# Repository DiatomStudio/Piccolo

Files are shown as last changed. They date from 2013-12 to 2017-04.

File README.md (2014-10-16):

#Piccolo, the tiny cnc bot#

A pocket sized open source CNC-bot.

Using laser-cutting, off-the-shelf hardware and Arduino, you can make your own simple 3 axis robot. Attach a brush or pen to make a quick drawing robot, or extend Piccolo with sensors, custom toolheads, or by using multiple Piccolos together. Experiment with 2D or 3D digital fabrication at a small scale!

For more info please see [www.piccolo.cc](http://www.piccolo.cc)

[Piccolo Flickr Pool](http://www.flickr.com/groups/1929303@N21/)

[www.diatom.cc](http://www.diatom.cc)



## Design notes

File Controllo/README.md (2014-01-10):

# Controllo
----------------
Controllo is a standalone program that runs on your, pc , mac or linux machine. That lets you send your own SVG vector artworks or a series of pre-defined generative artworks to your Piccolo for drawing.

Your Piccolo will need to have the usbTether firmware installed and be attached to your computer in order to communicate with Controllo. The usbTether program can be found in [PiccoloLib](https://github.com/DiatomStudio/Piccolo/tree/master/PiccoloLib) under examples.
 

####installing
- Download Controllo_current.zip
- Unzip and run the appropriate application for your system.

####how to use
- Load your own svg or select a generative pattern using the buttons on the left. 
- Lower your piccolo's drawing impliment to the paper using either the thumbwhere on the side of the Piccolo or the UP_ DOWN_ buttons in Controllo.
- Press the STARRT button or button_1 on your Piccolo to start drawing. 

####hacking
Controllo is written using the Processing programming language. If you would like to make your own changes you will need.

- Processing: <http://processing.org/>

the following processing libraries

- controlP5: <http://www.sojamo.de/libraries/controlP5/>
- Geomerative: <http://www.ricardmarxer.com/geomerative/>

####notes
To correctly draw imported SVG drawings, SVG's should be exported with all lines expanded and no compound shapes. 

The svg size should be less than 300 x 300 px. 

Piccolo should be connected to your computer via usb before starting Controllo. 

Controllo and it's source code is a work in progress, most functions work however there will some bugs.

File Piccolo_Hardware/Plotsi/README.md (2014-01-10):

## Plotsi

Plotsi is a series of earlier Piccolo designs that started as 3d printed parts and changed to be laser cut.
Rather than the X > Y > Z configuration of the Telaio and Piccolo v1 versions, the Plotsi designs put the Y axis mounted on Z axis, ie: X > Z > Y.

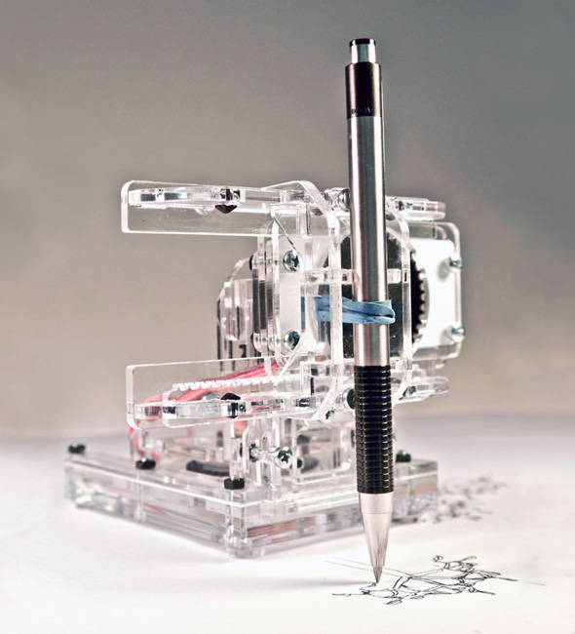
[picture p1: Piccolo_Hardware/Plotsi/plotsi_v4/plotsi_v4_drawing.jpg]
plotsi


---

### Plotsi v1

Early concept block-model looking at the dimensions of submicro servos and range of motion.  A speculative "cnc shield" for an arduino.  Not a working model, but could be with a bit of work.

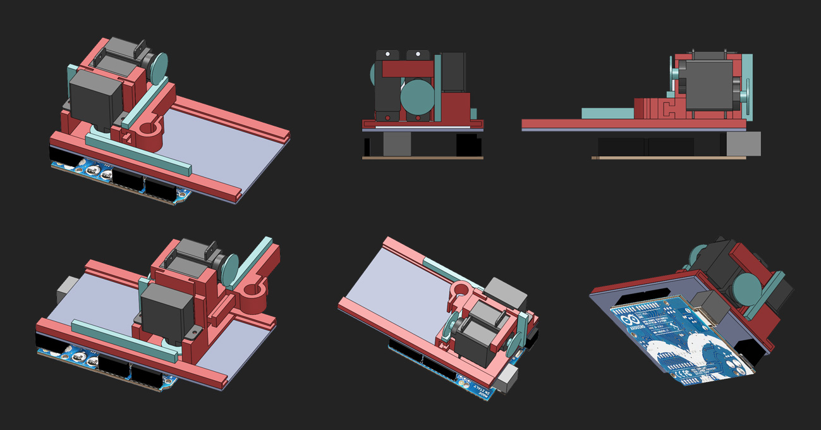
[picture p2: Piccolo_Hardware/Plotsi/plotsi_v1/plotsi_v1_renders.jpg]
plotsi-v1


---

### Plotsi v2

3D printable prototype, printed on on a makerbot cupcake cnc and with cheap generic analog servos (towerpro sg50-like).  Has a small 25x25x25mm output envelope.
[Youtube playlist of prototype in action](http://www.youtube.com/watch?v=IYrCUkX8gOE&list=PLRpx_txK6uzyulC7kqCXAvBz_-7jgT4Fn)

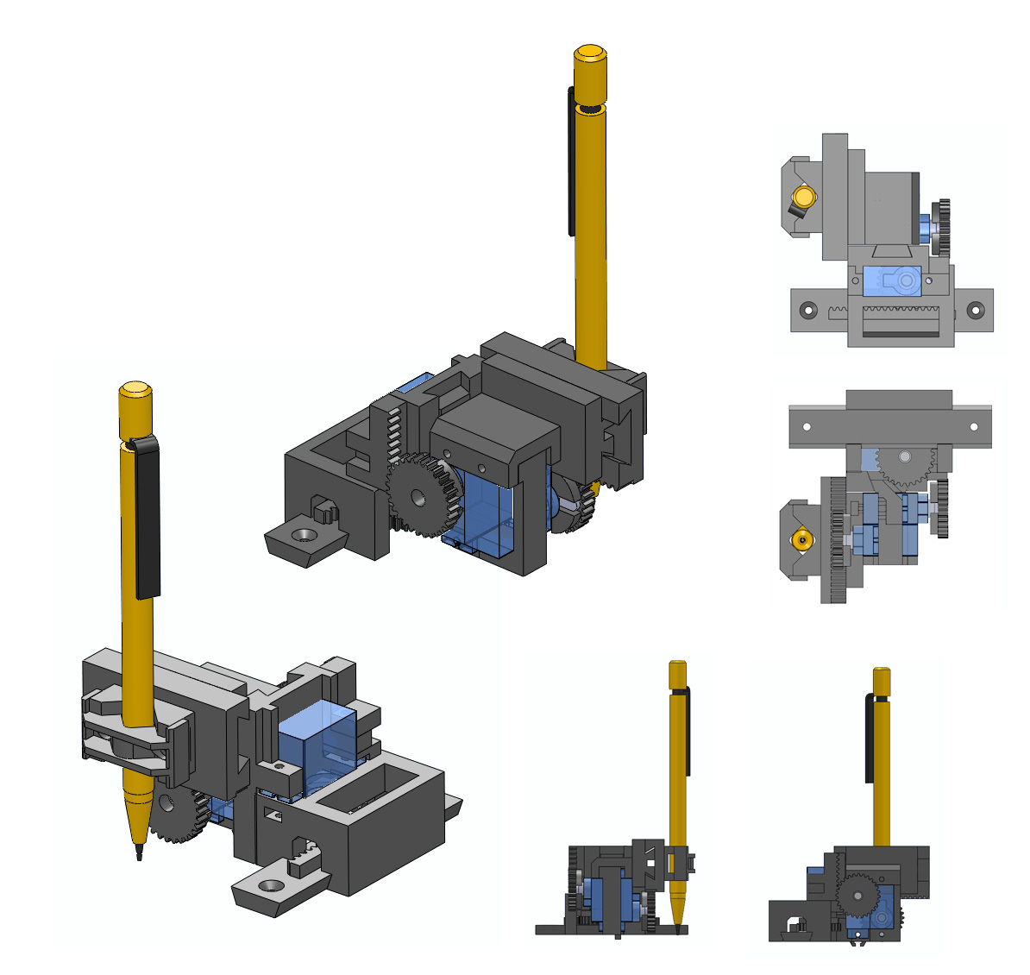
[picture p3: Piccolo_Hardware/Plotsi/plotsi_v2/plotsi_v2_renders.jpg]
plotsi-v2


---

### Plotsi v3

3D printable, also prototyped on a cupcake cnc but with less cheap emax digital ES08D servos.  Considerably larger than v2 with an output envelope of around 50x50x30mm roughly.

Used for an [installation at Tangíveis Resiência AZ](http://blog.diatom.cc/piccolo/piccolo-prototype-plotsi-at-tangiveis-residencia) in 2012, together with Teresa Cardoso.

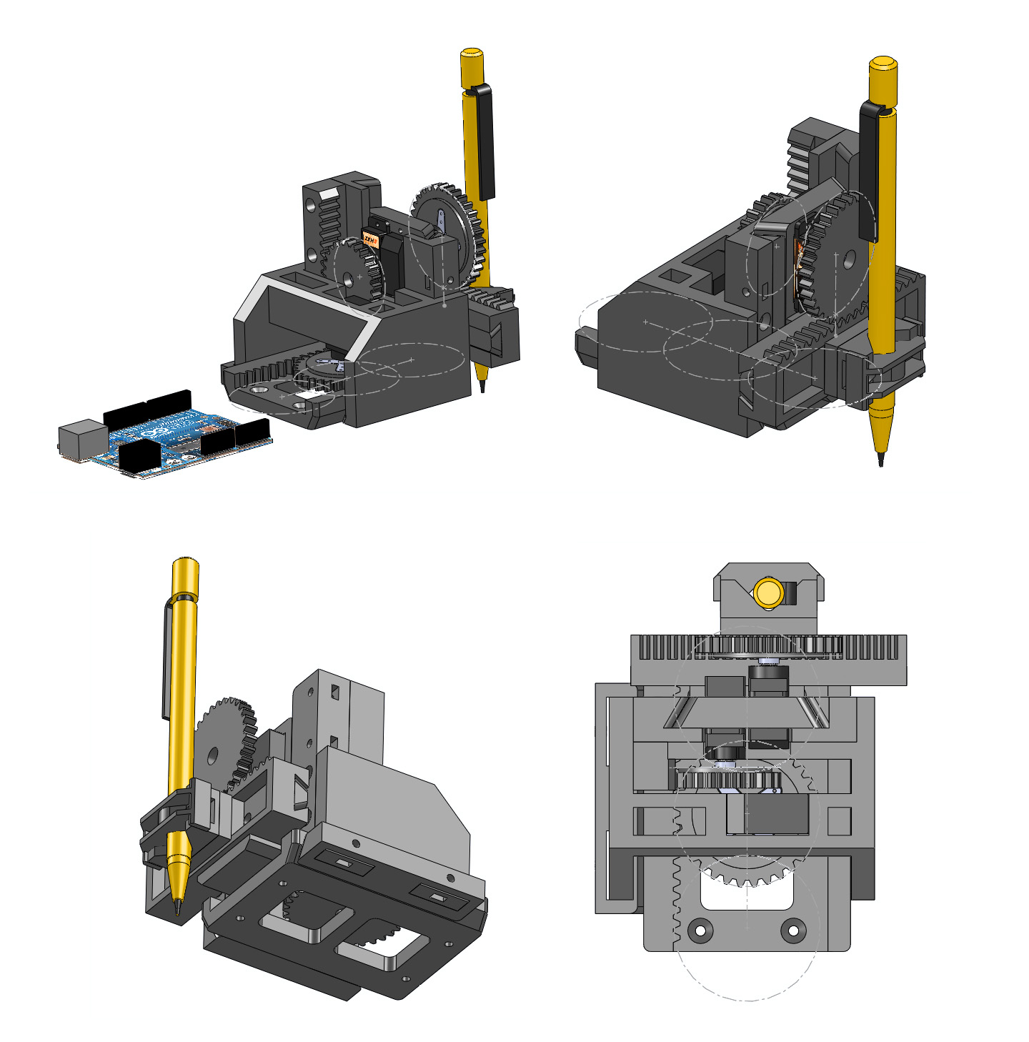
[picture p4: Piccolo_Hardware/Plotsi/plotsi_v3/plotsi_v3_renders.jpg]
plotsi-v3


---

### Plotsi v4

Laser cut design published with the initial launch of [](www.piccolo.cc).  Uses the same emax servos and has a larger 65x65x30mm output envelope.  This was our first widely prototyped Piccolo version.

[Winner of the TEI 2012 design challenge](http://blog.diatom.cc/piccolo/piccolo-wins-the-tei-design-challenge)

[Initial Piccolo cnc video](https://vimeo.com/36869769)

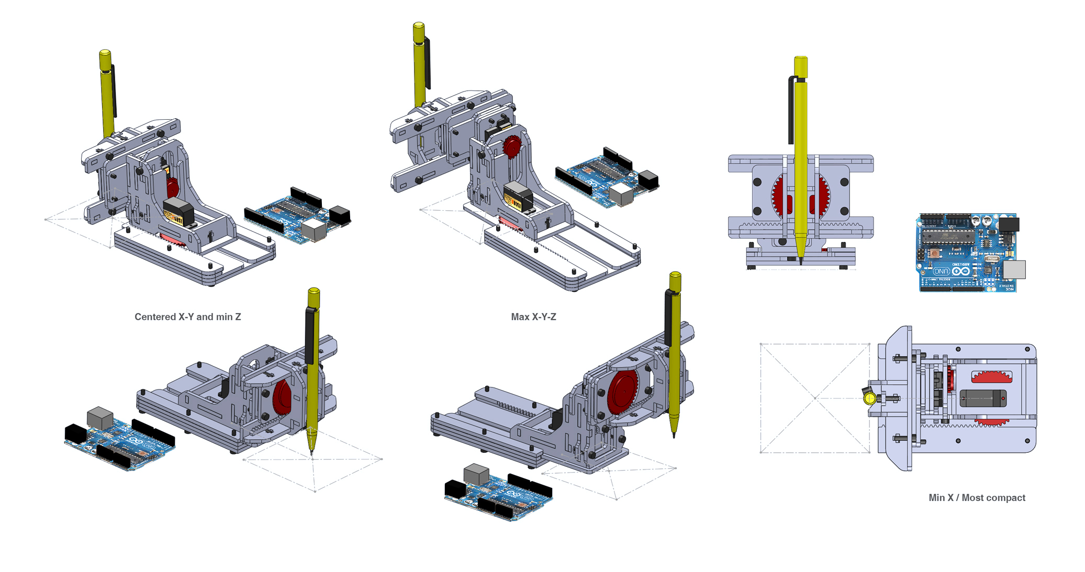
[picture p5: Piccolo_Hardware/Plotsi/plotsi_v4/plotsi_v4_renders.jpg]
plotsi-v4


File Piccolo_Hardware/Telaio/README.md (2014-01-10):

## Telaio

Telaio ("frame") follows an X > Y > Z configuration that stacks the X and Y gears on top of each other.  This is the strategy that led to the Piccolo v1 design.

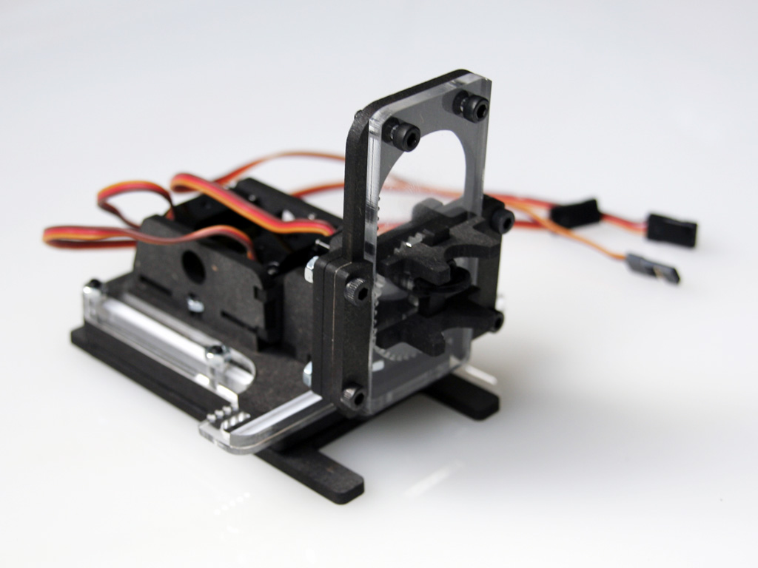
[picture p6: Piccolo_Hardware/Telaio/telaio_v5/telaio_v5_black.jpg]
telaio


---

### Telaio v0 / v1 / v2

These initial prototypes/concepts started with just the X/Y axis to create a simple servo-driven plotter.  The first was prototyped on a papercutter, the second was laser-cut.

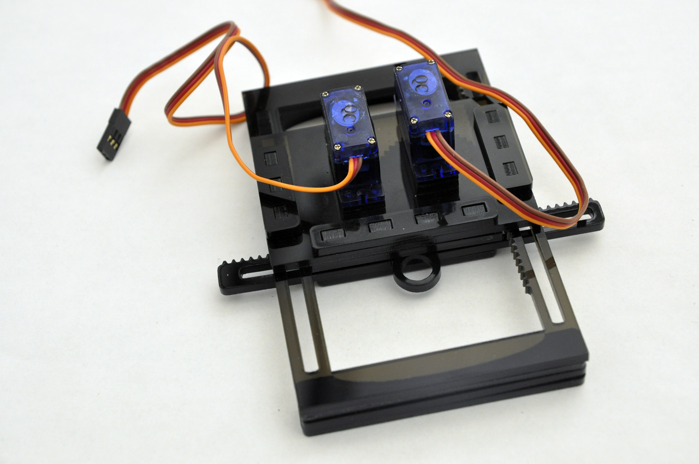
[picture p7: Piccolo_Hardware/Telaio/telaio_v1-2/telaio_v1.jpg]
telaio-v1


---

### Telaio v3 / v4

Laser-cut iterations using emax ES08D digital servos.

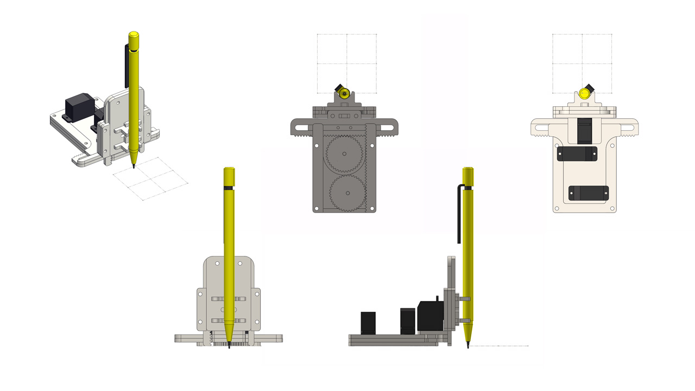
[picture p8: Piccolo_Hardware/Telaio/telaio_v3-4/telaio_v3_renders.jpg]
telaio-v3

_Telaio v3_

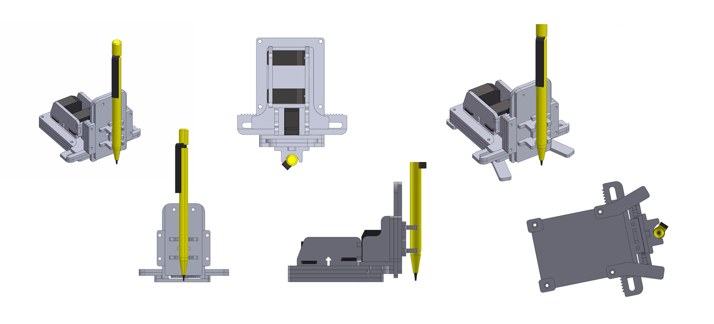
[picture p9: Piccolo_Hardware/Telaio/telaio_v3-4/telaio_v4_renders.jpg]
telaio-v4

_Telaio v4_

---

### Telaio v5

Smaller/more resolved laser-cut version, still using the ES08D servos.  The smallest of all our piccolo designs, but with an output envelope of about 60x60x40mm.

This design was used at our first piccolo workshop at the [LiWoLi 2012 festival in Linz](http://blog.diatom.cc/piccolo/build-your-own-piccolo-workshop-at-linz).  In the archive there are two versions of the design, one using M2 cap screws and one using more common, M3 ones.  As with Piccolo v1, we reccomend using a combination of MDF and acrylic as shown in the photo to help reduce friction.

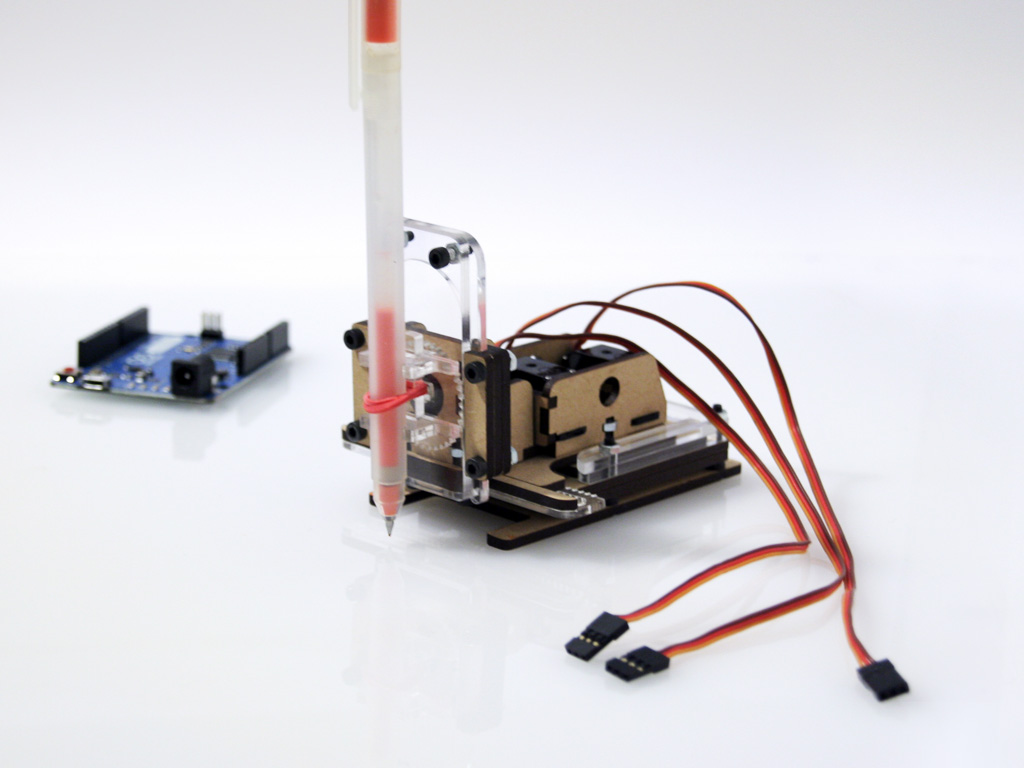
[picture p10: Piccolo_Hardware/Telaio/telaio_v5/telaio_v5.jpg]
telaio-v5


---

### Telaio v6

Laser-cut iteration that is a scaled-up version of v5 and using Corona DS-929MG servos.  We also integrated a Sparkfun Pro Micro into the base with a small protoboard for hooking up the servos, creating a 'stand-alone' design.  The output envelope is similar to the v5, about 60x60x45mm.

We used this design at our make-your-own-piccolo workshop at TEI 2013 in Barcelona.

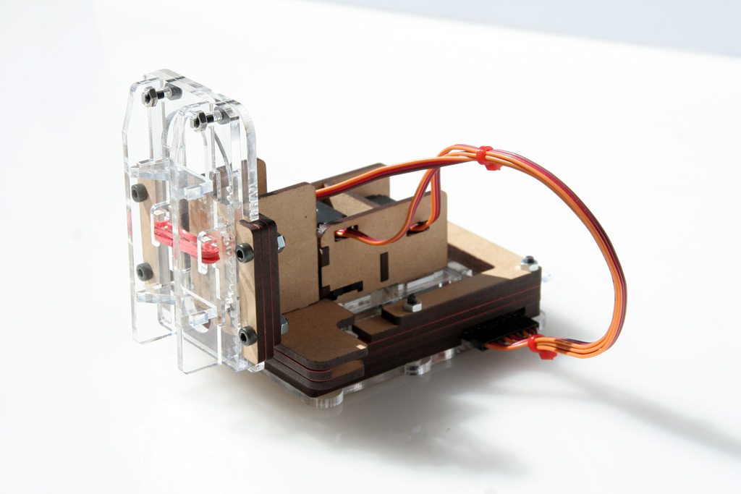
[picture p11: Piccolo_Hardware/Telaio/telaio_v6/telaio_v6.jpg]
telaio-v6


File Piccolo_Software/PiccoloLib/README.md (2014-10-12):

#PiccoloLib#

PiccoloLib is a library for [Arduino](http://www.arduino.cc) that makes it simple to program a Piccolo.

For an overview of PiccoloLib basics, take a look at [Getting Started](../../../../wiki/Getting-Started)

* Control movement, speed and accuracy.
* Various shape drawing functions.
* Configure & calibrate Piccolo.
* Send Piccolo co-ordinates over serial.
* [UsbTether](PiccoloLib/examples/usbTether/usbTether.ino) example lets you control piccolo from Processing using the PiccoloP5 library.
* Configure axes individually with PiccoloAxis class, or add additional axes.

---

##Installation##

1. Download PiccoloLib_current.zip
2. Open the zip in Arduino by: Sketch > Import Library > Add Library

Alternatively, you can extract the archive into into your Arduino libraries folder manually.
If you are not sure where your libraries folder is, have a look at the Arduino libraries guide: http://arduino.cc/en/Guide/Libraries

---

##Reference##

Piccolo's output is intended to be used in mm, however you can scale the output to any arbitrary units using *calibrate()*.

###PiccoloLib Class###

---
####Setup, Configuration & Motion####

`void setup()`  
Sets up piccolo using the default pin assignments for the servos:  
X pin 3  
Y pin 5  
Z pin 6

`void setup(int xPin, int yPin, int zPin)`  
Set up piccolo using custom pins assignments.

`void invert(boolean invertX, boolean invertY, boolean invertZ)`  
Invert the output on any of the axes.

`void moveCenter(float xOffset, float yOffset)`  
`void moveCenter(float xOffset, float yOffset, float zOffset)`  
Adjust piccolo's zero position.

`void calibrate(float targetDimension, float actualX, float actualY)`  
`void calibrate(float targetDimension, float actualX, float actualY, float actualZ)`  
Use this to scale piccolo's output, which you can use to calibrate its accuracy.  First draw a square (or cube) of *targetDimension*, then measure the output and put *calibrate()* into your *setup()* with these dimensions as *actualX*, *actualY* etc.

`void setBedSize(float size)`  
`void setBedSize(float xySize, float zSize)`  
`void setBedSize(float xSize, float ySize, float zSize)`  
Will set the minimum and maximum positions of each axis, therefore defining the overall bed size.

`void setSpeed(float speed)`  
Defines piccolo's movement speed when using vertex() or shape functions.  In mm per second.  Default speed is 60mm/s.

`void setStepSize(float _stepSize)`  
Steps are used to control piccolo's motion and speed.  The default step size is 0.1mm.  A smaller step size means a more controlled motion, but too small will limit the maximum speed.  
This also affects curvature when using *ellipse()*, *arc()*, or *bezier()* - a smaller stepSize means a less faceted curve

`int drawOrientation`  
`void setDrawOrientation(int _orientation)`  
**_Work in progress._** Rotates the output:  
0 - default, drawing with bottom of drawing to the left.  
1 - top, as if piccolo is drawing upside down.  
2 - right, drawing with the bottom of the drawing to the right.  
3  - bottom, as if piccolo is drawing the correct way up.  

`boolean disableMotion`  
Disables servo motion, for debugging purposes.

---
####Piccolo Inputs####

`float readThumbwheel()`  
Returns a value from 0 to 1023 based on the position of the thumbwheel.

`boolean buttonOneDown()`  
Returns true if button one is pressed.

`boolean buttonTwoDown()`  
Returns true if button two is pressed.

---
####Mechanical Control####

`void moveX(float x)`  
`void moveY(float y)`  
`void moveZ(float z)`  
`void move(float x, float y)`  
`void move(float x, float y, float z)`  
Sends the servo(s) to a position.  They will respond at their maximum speed, and you may need to allow time for the servos to move in your code with *delay()*.

`void home()`  
Moves piccolo to (X minimum, 0, pen-up position).

`void thumbwheelControlX()`  
`void thumbwheelControlY()`  
`void thumbwheelControlZ()`  
Will move piccolo in each axis based on the thumbwheel position, between the minimum and maximum.

`void setPenDownPos(float _penDownPos)`  
`float getPenDownPos()`  
Set or retrieve the pen-down position.

---
####Making Shapes####

In general all drawing commands follow the same format as Processing drawing commands, for more info on these please visit: http://processing.org/reference/

`void beginShape()`  
Moves piccolo to the first vertex and then lowers the pen to the pen-down position.  
`void endShape()`  
Raises the pen to the pen-up position.  

`void vertex(float x,  float y)`  
`void vertex(float x,  float y,  float z)`  
Moves piccolo to (x,y,z) using the step size and speed to control the motion.

`void line(float x1, float y1, float x2, float y2)`  
`void line(float x1, float y1, float z1, float x2, float y2, float z2)`  
`void rect(float x,  float y,  float width, float height)`  
`void rect(float x,  float y,  float z, float width, float height)`  
`void ellipse(float x,  float y,  float width, float height)`  
`void arc(float x , float y , float width, float height, float startA, float stopA)`  
`void bezier(float x1, float  y1, float  cx1, float  cy1, float  cx2, float  cy2, float  x2, float  y2)`  
`void bezierYZ(float x1, float  y1, float  cx1, float  cy1, float  cx2, float  cy2, float  x2, float  y2)`  
`float bezierPoint(float a, float b, float c, float d, float t)`  
`float bezierTangent(float a, float b, float c, float d, float t)`  

---
####Serial Communication####

`void serialSetup()`  
Opens a serial port at 115200 baud. ready for Piccolo instructions from Controllo or another host device. This is only needed if Piccolo is controlled remotely. 

`void serialLoop()`  
Main Serial loop, this should be called in program main loop to check for waiting piccolo instructions on the serial port. This is only needed if Piccolo is controlled remotely via Controllo or another host device. 

`boolean serialStream`  
A debug flag used to stream Piccolo's move coordinates back over serial for rendering in Controllo.  
This is also useful for retrieving coordinates from Piccolo to debug your toolpath.

---
###PiccoloAxis class###

Each servo is controlled as a PiccoloAxis object.  
*uS = pulse width in microseconds of signal sent to the servo.*

---
####Variable Heirarchy####

1. `uScenter` - Defines the center position of the servo, based on where we want piccolo think the center is.  Normally this would be mid-way between the minimum and maximum rotation of the servo.  Default is 1551uS.  
`bedSize` - We define what we want the bed size to be.  The default is 50mm, which is a conservative size that should fit within the range of most DS929-MG servos.  
`uSdeg` - We specify the change in uS per degree of rotation for the servo. This can be calibrated as in 5.  Default is 9.7 us/deg.  
`gearSize` - We specify the gear pitch diameter based on the actual pinion gear dimensions.  Default is 35.23mm.

2. The gear pitch diameter and the change in uS per degree are used to calculate the change in uS per mm of motion:  
`uSmm = uSdeg/((PI/360)*gearSize)`

3. The uS range is found by multiplying the bed size by the uS/mm:  
`uSrange = bedSize * uSmm`

4. The uS minimum and maximums are found by using the uS range and center:  
`uSmin = uScenter - (uSrange/2)`  
`uSmax = uScenter + (uSrange/2)`

5. uSdeg can be calibrated by drawing a target dimension and measuring the actual output:  
`uSdeg  = ((target*uSmm)/actual) * (PI/360)*gearSize`

---
####Setup, Configuration & Motion####

`void setup(int _pin)`  
`void setup(int _pin, int _uScenter, float _bedSize)`  
`void setup(int _pin, int _uScenter, float _bedSize, float _uSdeg)`  
`void setup(int _pin, int _uScenter, float _bedSize, float _uSdeg, float _gearSize)`  
`void setup(int _pin, int _uScenter, float _bedSize, float _uSdeg, float _gearSize, boolean _inverted)`

`void calcuSmm()`  
`void calcuSrange()`  
`void calcMinMax()`  
`void calcuSdeg(float target, float actual)`

`void invert(boolean _inverted)`  
`void moveCenter(float offset)`  
`void setBedSize(float newSize)`  
`void move(float _pos)`  

---
####Helper Functions####

`int getPin()`  
`int getuScenter()`  
`float getuSdeg()`  
`float getGearSize()`  
`float getBedSize()`  
`float getuSmm()`  
`int getuSrange()`  
`int getuSmin()`  
`int getuSmax()`  
`float getPos()`  
`boolean isInverted()`

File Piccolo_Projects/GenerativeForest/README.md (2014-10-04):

# Generative Forest
A Piccolo Project 
----------------

Piccolo is a pocket-sized stand-alone CNC platform.  For more info please see [www.piccolo.cc](http://www.piccolo.cc)

####About: 
Piccolo draws a generative forest across a table top.

Piccolo draws generative plants and trees using a light sensor as it's input. When Piccolo is placed under a bight light, taller and more bushy tree is generated and drawn while lower light levels or shadows result in small shrubs and grasses. 

####You Will Need:

- 1 x Piccolo
- 1 x LDR (Light dependent resistor)
- 1 x Resistor matching maximun LDR value e.g.e 10K 

- PiccoloLib (tested with v0.8)
- GenerativeForest Arduino sketch

####Assembley: 

Wire your LDR with one leg connected to the A2 input on the side of your piccolo and the other connected to GND, now take your resistor and connect one end to VCC and the other also to A2.

This has created a voltage divider so if more light is hits the LDR it's resistance will lower allowing current to flow into GND instead of A2 a darker environment will cause the LDR's resistance to raise and more current to flow into A2 resulting in  a higher reading. 

The LDR can be placed at other points on Piccolo for example the Z-Axis by soldering wires to it's legs. 

Make sure PicccoloLib is installed correctly and upload the GenerativeForest Sketch to piccolo. 

####Usage: 

- Add a drawing implement to Piccolo and set the drawing height using the thumb wheel. 
- Place Piccolo under the darkest point of light on the surface and hold down button two for two seconds (the button next to the usb plug) this calibrates you light sensor.
- Move piccolo onto a surface and press button one to start drawing a generative tree.

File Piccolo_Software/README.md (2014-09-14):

# Piccolo Software
----------------

### Controllo
----------------
Controllo is a standalone program that runs on your, pc , mac or linux machine. That lets you send your own SVG vector artworks or a series of pre-defined generative artworks to your Piccolo for drawing.

### PiccoloLib
----------------
PiccoloLib is a Arduino library for controlling Piccolo using Arduino and Processing like drawing calls. 

#####usbTether src
PiccoloLib includes an example program (sketch) 'usbTether'. This sketch needs to be uploaded to your Piccolo in order to use Controllo or PiccoloP5 with your Piccolo. 

### PiccoloP5
----------------
PiccoloP5 is a Processing library for controlling your Piccolo from your computer in real time. Processing drawing commands can be sent to your Piccolo for drawing. 

#####Controllo src
Controllo is included as example in the PiccoloP5 library.

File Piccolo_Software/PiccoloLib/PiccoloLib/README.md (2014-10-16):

##PiccoloLib v0.81  
*Arduino library for controlling Piccolo, the tiny CNC-bot.*  

Piccolo.cc  
Created by Diatom Studio, October 10, 2013.  
Released into the public domain.  

##Changes:

###0.82  
- Fixing bugs in examples.
- Removed incompatible examples. 

###0.81  
-  Minor restructuring of comments. 
-  Added bezier(y,z) function
-  Commented out unused Piccolo Axis functions.s

###0.8  
-  Major restructuring of code. 
-  Added Axis objects to store and calculate Axis positions. 

###0.21  
-  Reverted BeginShape and EndShape back to BeginDraw and EndDraw to bring them in line with processing.org
-  Changed received coordinates from human readable chars to signed 32 bit ints backed into 4 bytes. This make our ranges larger, supports negative numbers and we send less data. 

###0.2  
-  Start of change tracking.

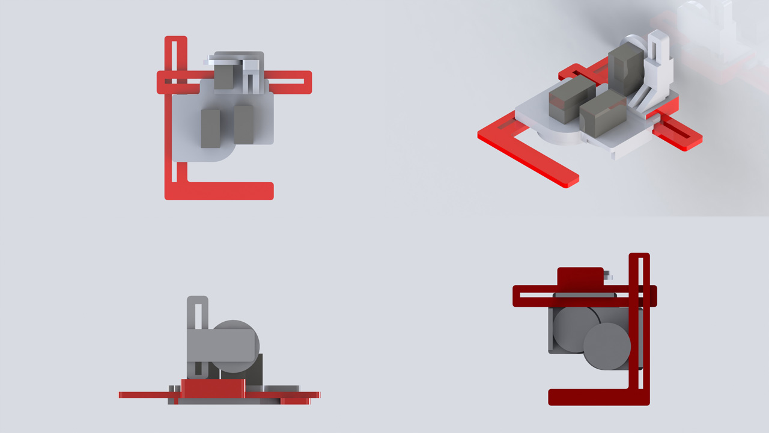
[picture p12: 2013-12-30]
Piccolo_Hardware/Telaio/telaio_v1-2/telaio_v2_renders.jpg

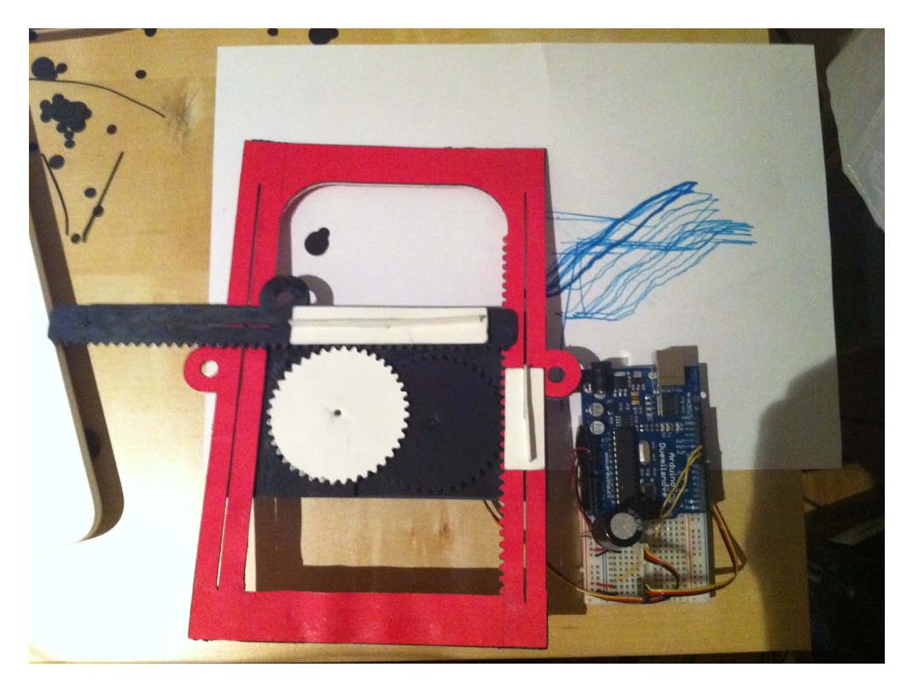
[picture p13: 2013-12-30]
Piccolo_Hardware/Telaio/telaio_v1-2/telaio_v0.jpg

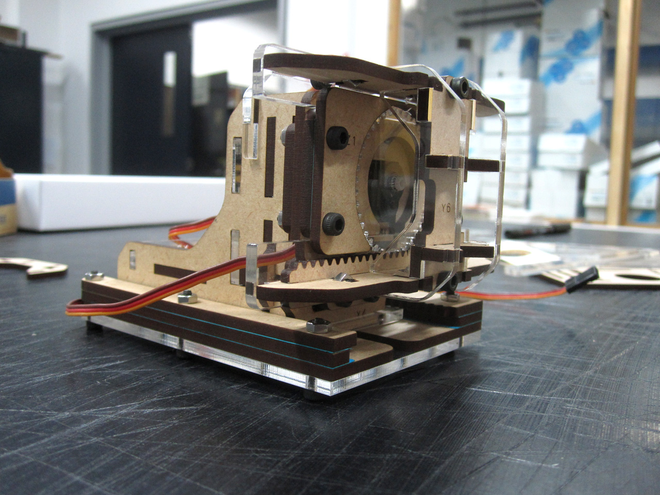
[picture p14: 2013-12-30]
Piccolo_Hardware/Plotsi/plotsi_v4/plotsi_v4.jpg

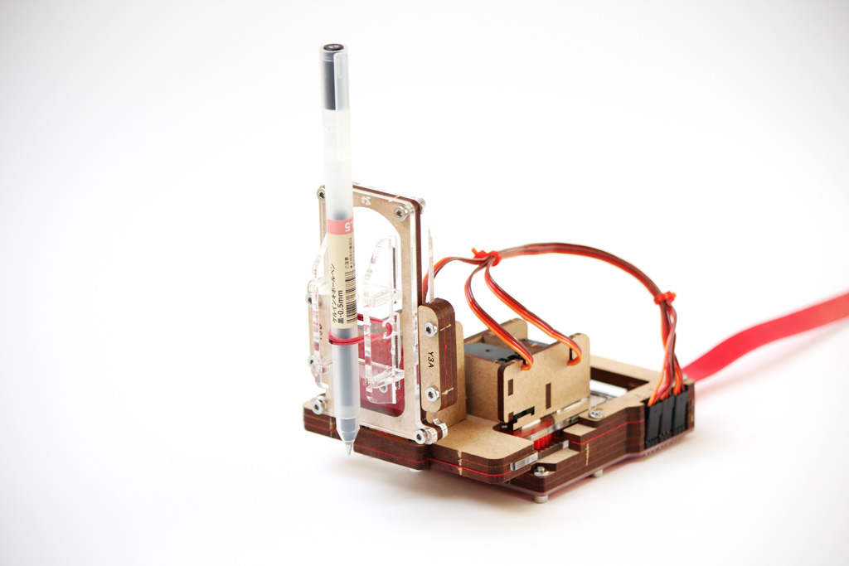
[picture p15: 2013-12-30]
Piccolo_Hardware/Piccolo_v1/piccolo_v1.jpg

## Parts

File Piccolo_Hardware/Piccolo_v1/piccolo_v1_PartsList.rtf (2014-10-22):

Piccolo v1 Parts List

Servos
3x Corona DS-929MG
http://www.servodatabase.com/servo/corona/ds-929mg

Material
3mm Acrylic, about 200 x 200
3mm MDF, about 200 x 270
Heavy Paper, about 160gsm, about 150 x 130

Fasteners

Metric Sockethead Cap Screws :

8x M3 10mm with low profile head
3x M3 16mm with low profile head
2x M3 10mm with normal head
4x M3 22mm with normal head
17x M3 low profile nuts

1 x rubber bands

PCB
Piccolo PCB v0.9 (uses Sparkfun Pro Micro), or other Arduino compatible microcontroller.
R/A female headers (optional - may be needed for assembly. See Piccolo PCB v0.9 Assembly https://github.com/DiatomStudio/Piccolo/wiki/Piccolo-Assembly-Instructions#wiki-piccolo-pcb-v09-assembly)
2x08
http://www.digikey.com/product-detail/en/M20-9963645/952-2251-ND/3728215
3x Capacitors
330uF Panasonic ECE-A0JKS331
http://www.digikey.com/product-detail/en/ECE-A0JKS331/P959-ND/160539
2x Buttons
3.5mm R/A tactile switch, C&K Components PTS635VL39 LFS
http://www.digikey.co.uk/product-detail/en/PTS635VL39%20LFS/CKN9099-ND/1146757
3x Servo Headers
1x03 male
http://www.digikey.co.uk/product-detail/en/PRPC003SAAN-RC/S1011EC-03-ND/2775251
1x Power Header
JST PH 2pos male R/A
http://www.digikey.co.uk/product-detail/en/S2B-PH-K-S(LF)(SN)/455-1719-ND/926626
1x GPIO Header
2x08 female R/A
http://www.digikey.co.uk/product-detail/en/PPTC082LJBN-RC/S5522-ND/775980
1x Thumbwheel Potentiometer
10k Ohm Linear
https://www.sparkfun.com/products/11173

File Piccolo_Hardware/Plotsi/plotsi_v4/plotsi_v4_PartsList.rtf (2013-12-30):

Piccolo - Plotsi V4 Parts List

Servos
3x EMAX es08D
http://www.servodatabase.com/servo/emax/es08d

Material
3mm Acrylic, 265 x 110mm
2mm Acrylic, 95 x 70mm
3mm MDF, 235 x 335mm
Heavy Paper, about 160gsm. 1x A4

Fasteners
M3 Socket Head Cap Screws
16 x 16mm, 9 x 12mm
25 x M3 Nuts
1 x rubber band

Operation
Arduino Uno or similar
4.8-6V Power supply (optional, may be required for stable operation of the servos)
large (>100uF) electrolytic capacitor (optional - by putting across GND and servo-voltage, can help reduce jitter)

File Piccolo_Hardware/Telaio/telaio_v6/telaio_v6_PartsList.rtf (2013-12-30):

Piccolo - Telaio V6 Parts List

Servos
3x EMAX es08D
http://www.servodatabase.com/servo/emax/es08d

Material
3mm MDF, 250 x 250mm
3mm Acrylic, 250 x 250mm
2mm Acrylic, 40 x 120mm
Heavy Paper, about 160gsm. 1x A4

Fasteners

Metric Sockethead Cap Screws :

using modified 3mm screw version:
3 x M3 16mm
4 x M3 20mm
6 x M3 12mm
13x M3 nuts

1 x rubber band

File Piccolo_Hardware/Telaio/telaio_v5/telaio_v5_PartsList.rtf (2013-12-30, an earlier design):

Piccolo - Telaio V5 Parts List

Servos
3x EMAX es08D
http://www.servodatabase.com/servo/emax/es08d

Material
3mm Acrylic, 180 x 180mm
2mm Acrylic, 60 x 110mm
Heavy Paper, about 160gsm. 1x A4

Fasteners

Metric Sockethead Cap Screws :

using original version
2x M2.5 3mm
1x M2.5 6mm
6x M2.5 12mm
6x M2.5 16mm
13x M2.5 nuts
2x M2 12mm
2x M2 nuts

using modified 3mm screw version:
2x M3 3mm
1x M3 6mm
8x M3 12mm
6x M3 16mm
15x M3 nuts

1 x rubber band

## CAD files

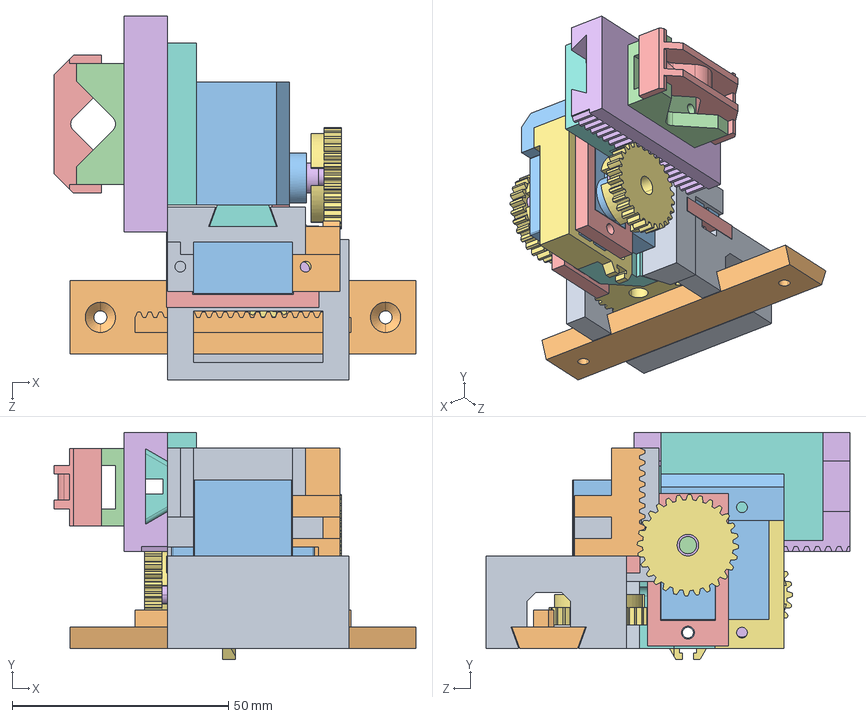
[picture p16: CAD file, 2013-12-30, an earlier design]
Piccolo_Hardware/Plotsi/plotsi_v2/plotsi_v2_assembled.STEP
83.7 x 52.5 x 84.2 mm
x-stage
Mauricio_Servo x 3
servogears x 3
z-stage

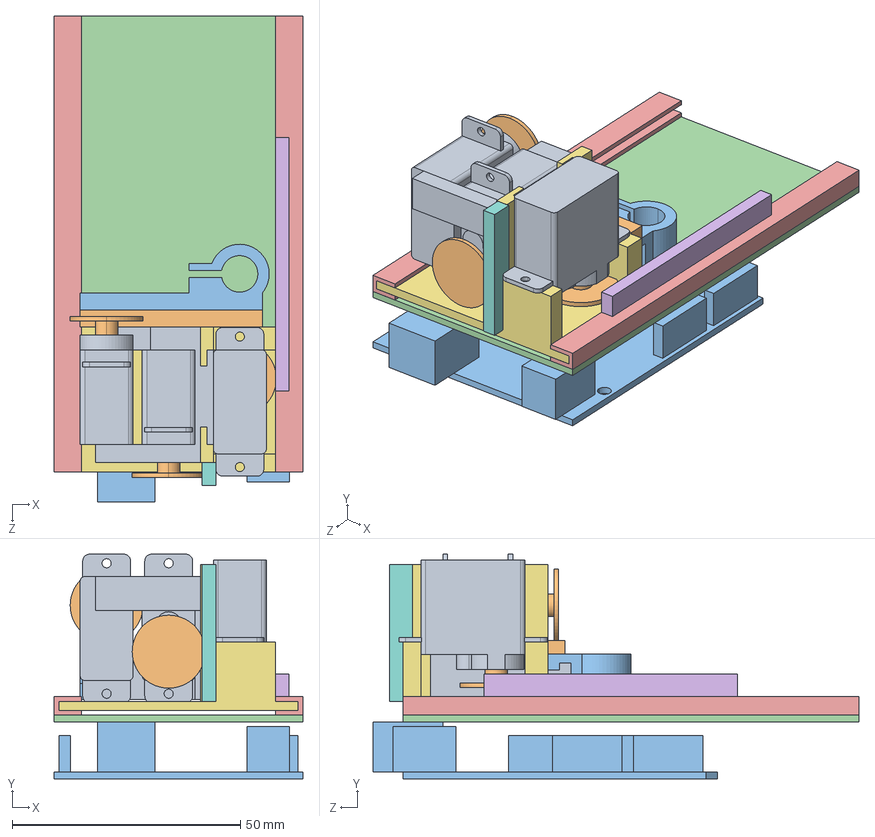
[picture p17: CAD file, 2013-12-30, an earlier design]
Piccolo_Hardware/Plotsi/plotsi_v1/plotsi_v1.STEP
54.5 x 49.3 x 106.5 mm
futuba_hs55 x 3
arduino
MockGantry1_pt1
MockGantry1_pt2
MockGantry1_pt3
MockGantry1_pt4

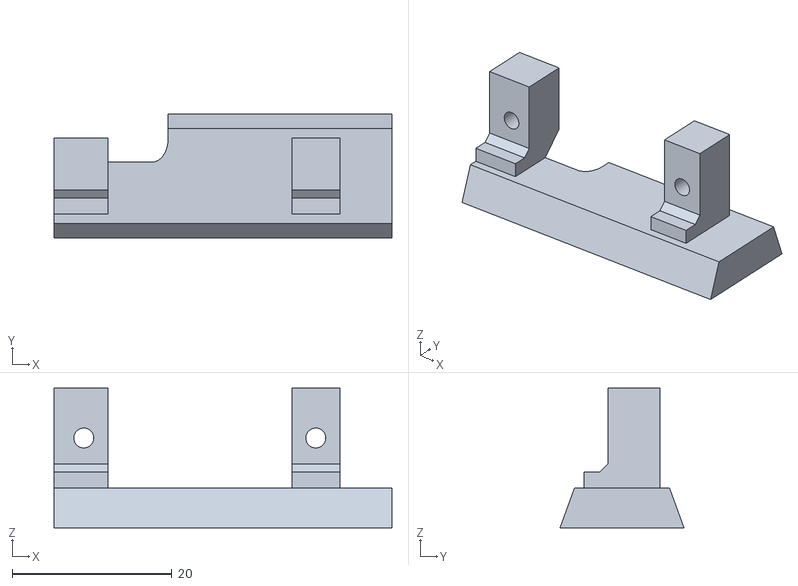
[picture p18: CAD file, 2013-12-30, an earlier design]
Piccolo_Hardware/Plotsi/plotsi_v2/parts/z-body-1.STL
42.2 x 15.5 x 17.5

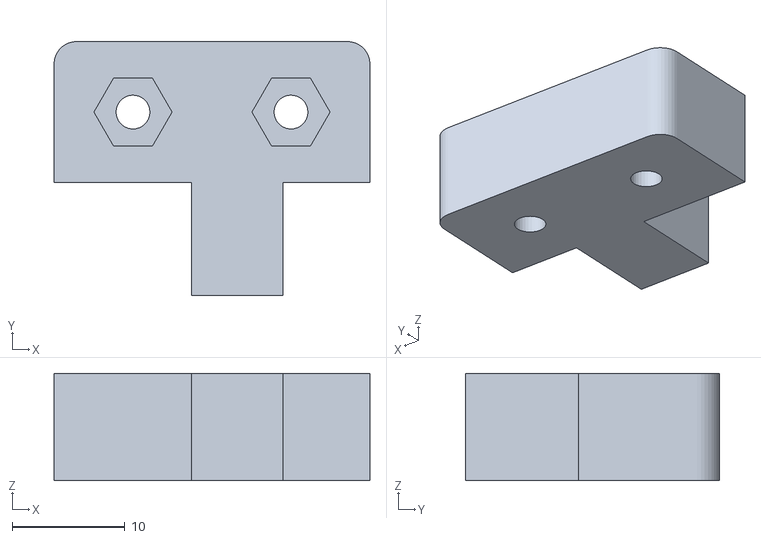
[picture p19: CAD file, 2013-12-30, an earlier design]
Piccolo_Hardware/Plotsi/plotsi_v3/parts/x-sliderA.STL
28.0 x 22.5 x 9.50

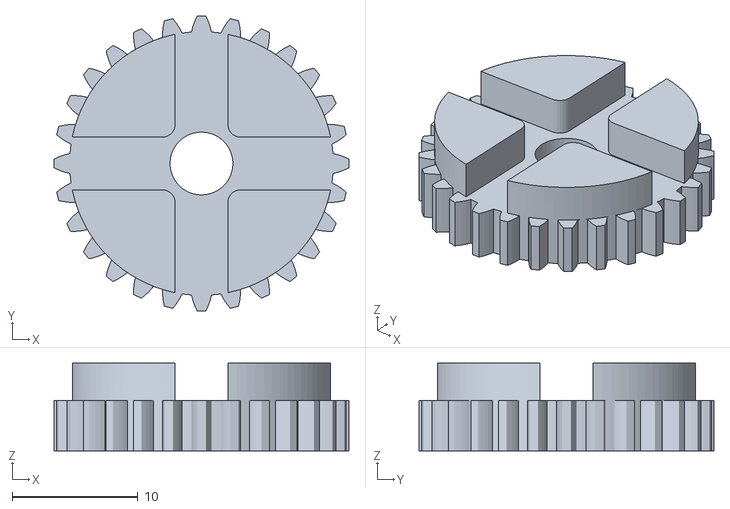
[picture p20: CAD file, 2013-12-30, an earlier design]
Piccolo_Hardware/Plotsi/plotsi_v2/parts/ServoGear_3mm_28tooth.STL
23.5 x 23.5 x 7.00

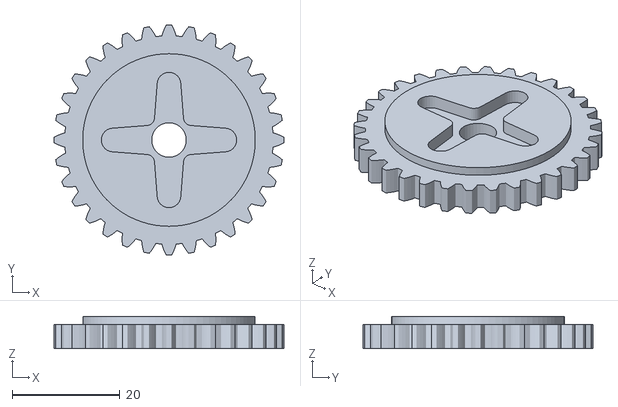
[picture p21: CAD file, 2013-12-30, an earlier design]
Piccolo_Hardware/Plotsi/plotsi_v3/parts/44tooth_gear.STL
42.6 x 42.6 x 6.00

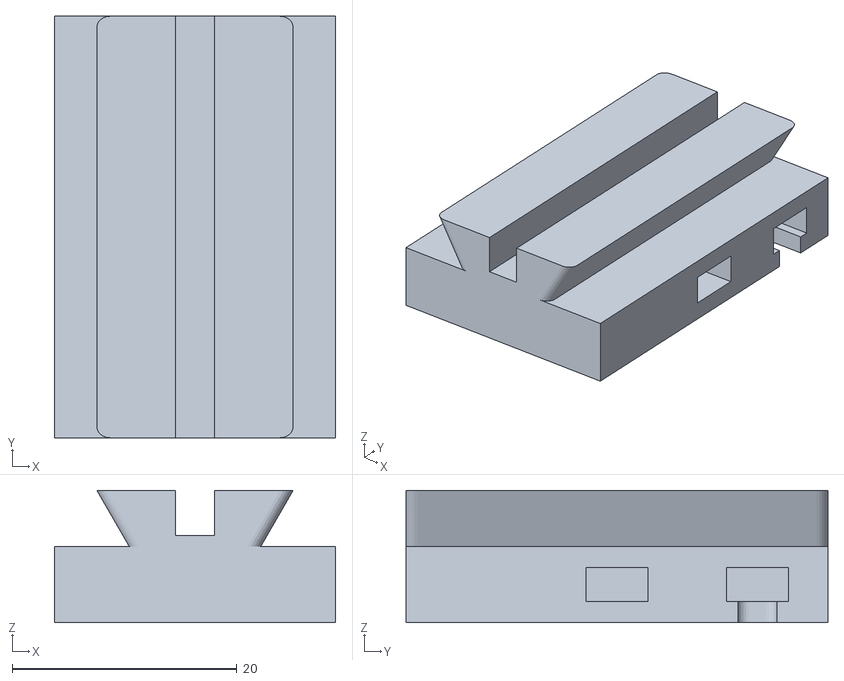
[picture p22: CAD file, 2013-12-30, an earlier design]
Piccolo_Hardware/Plotsi/plotsi_v2/parts/y-slider.STL
25.0 x 37.5 x 11.8

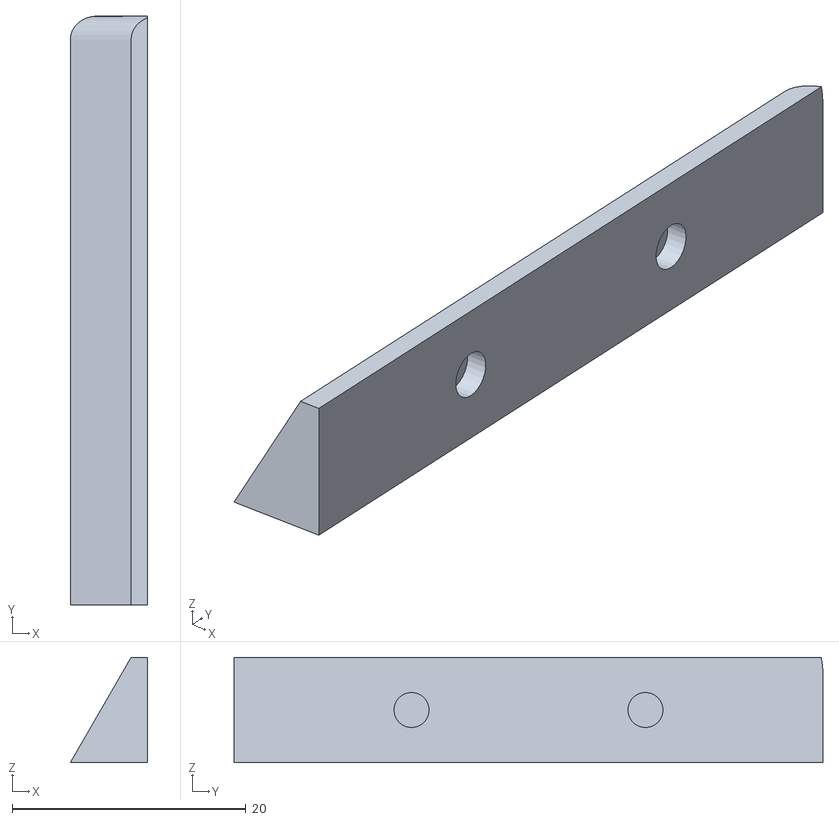
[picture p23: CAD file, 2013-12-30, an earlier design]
Piccolo_Hardware/Plotsi/plotsi_v3/parts/z-clamp.STL
6.62 x 50.4 x 9.00

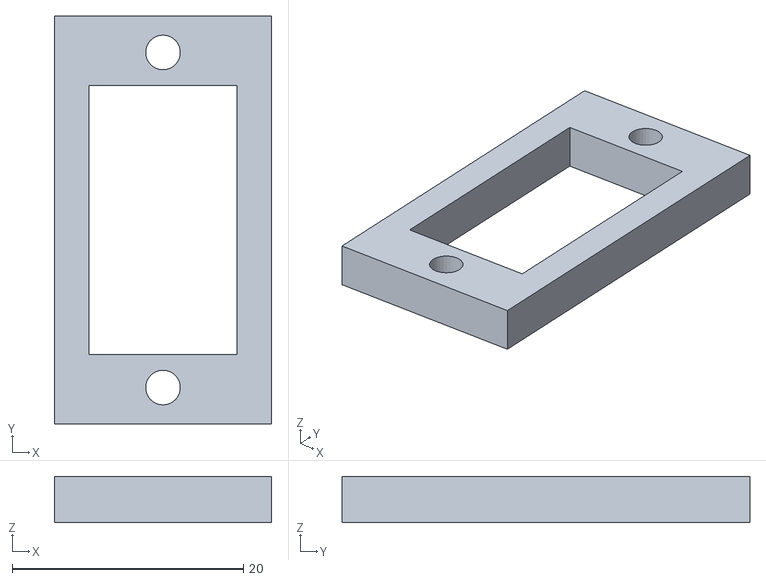
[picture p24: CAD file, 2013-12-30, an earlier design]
Piccolo_Hardware/Plotsi/plotsi_v2/parts/servo_drill_guide.STL
18.8 x 35.3 x 4.00

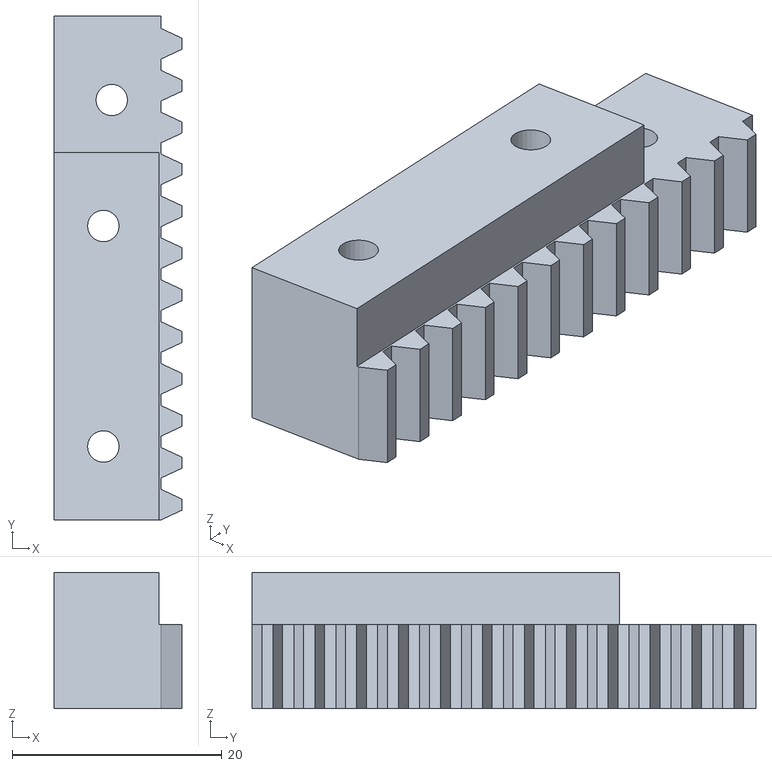
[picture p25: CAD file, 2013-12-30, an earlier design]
Piccolo_Hardware/Plotsi/plotsi_v3/parts/z-rack.STL
12.2 x 48.0 x 13.0

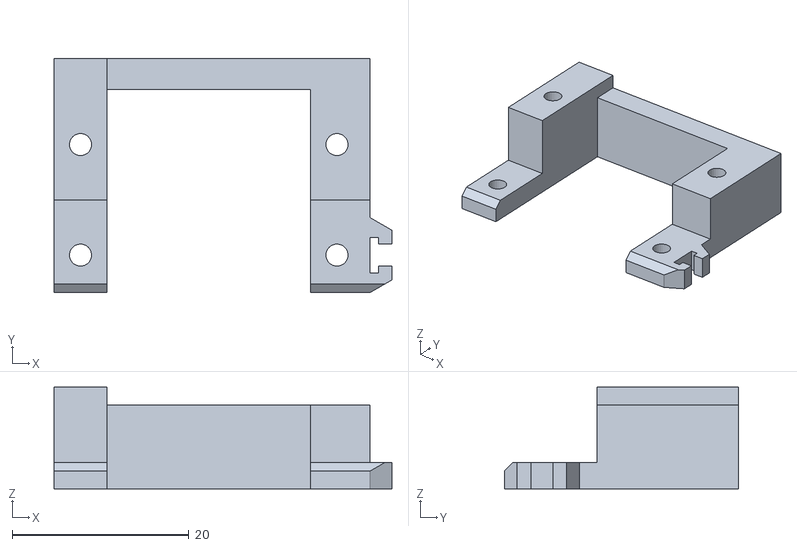
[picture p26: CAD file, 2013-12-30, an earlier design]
Piccolo_Hardware/Plotsi/plotsi_v2/parts/z-body-2.STL
38.2 x 26.5 x 11.5

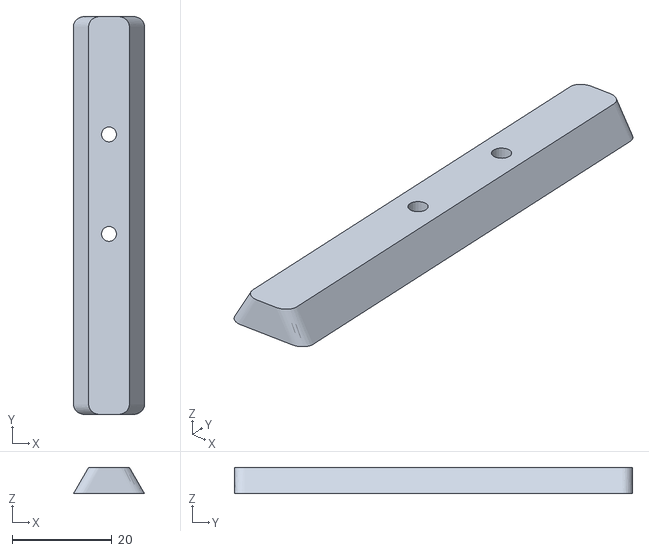
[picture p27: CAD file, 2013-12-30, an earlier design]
Piccolo_Hardware/Plotsi/plotsi_v3/parts/y-slider.STL
14.3 x 80.0 x 5.30

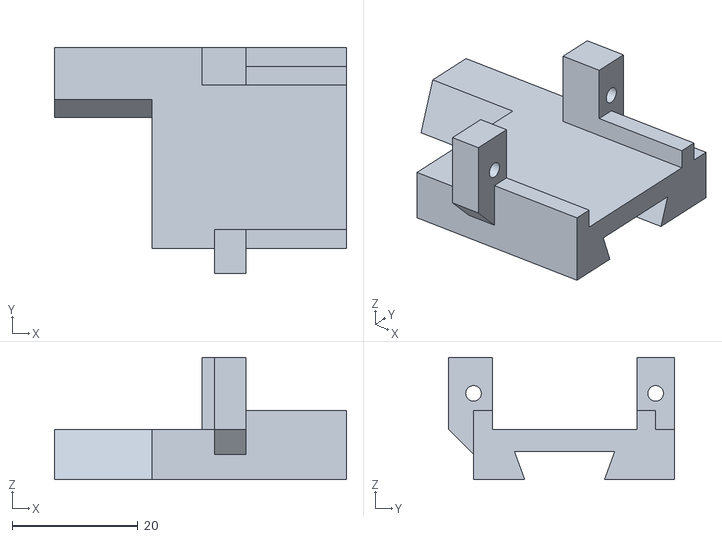
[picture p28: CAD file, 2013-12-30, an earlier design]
Piccolo_Hardware/Plotsi/plotsi_v2/parts/z-slider.STL
46.5 x 36.0 x 19.5

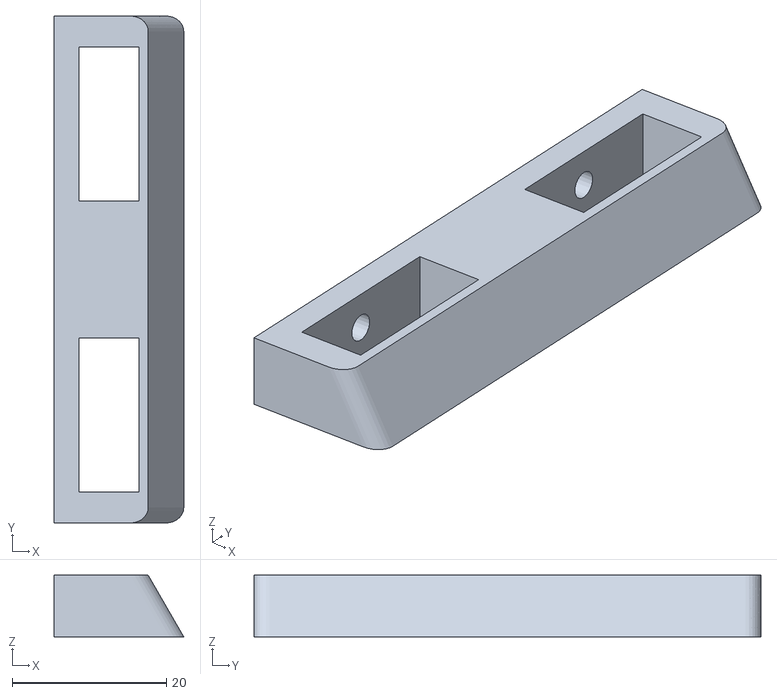
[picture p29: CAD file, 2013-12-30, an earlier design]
Piccolo_Hardware/Plotsi/plotsi_v3/parts/x-clamp.STL
16.8 x 65.8 x 8.00

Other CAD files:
Piccolo_Hardware/Plotsi/plotsi_v2/parts/y-rack.STL
Piccolo_Hardware/Plotsi/plotsi_v3/parts/body.STL
Piccolo_Hardware/Plotsi/plotsi_v2/parts/y-body.STL
Piccolo_Hardware/Plotsi/plotsi_v3/parts/x-sliderB.STL
Piccolo_Hardware/Plotsi/plotsi_v1/plotsi_v1.STL
Piccolo_Hardware/Plotsi/plotsi_v2/parts/head-base.STL
Piccolo_Hardware/Plotsi/plotsi_v2/parts/head-cap.STL
Piccolo_Hardware/Plotsi/plotsi_v2/parts/x-body.STL
Piccolo_Hardware/Plotsi/plotsi_v2/parts/x-rack.STL
Piccolo_Hardware/Plotsi/plotsi_v2/parts/y-stage.STL
Piccolo_Hardware/Plotsi/plotsi_v2/parts/z-rack.STL
Piccolo_Hardware/Plotsi/plotsi_v3/parts/24tooth_gear.stl
Piccolo_Hardware/Plotsi/plotsi_v3/parts/base.STL
Piccolo_Hardware/Plotsi/plotsi_v3/parts/drill guide.STL
Piccolo_Hardware/Plotsi/plotsi_v3/parts/head_spacer.STL
Piccolo_Hardware/Plotsi/plotsi_v3/parts/y-body.STL
Piccolo_Hardware/Plotsi/plotsi_v3/parts/y-rack.STL
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

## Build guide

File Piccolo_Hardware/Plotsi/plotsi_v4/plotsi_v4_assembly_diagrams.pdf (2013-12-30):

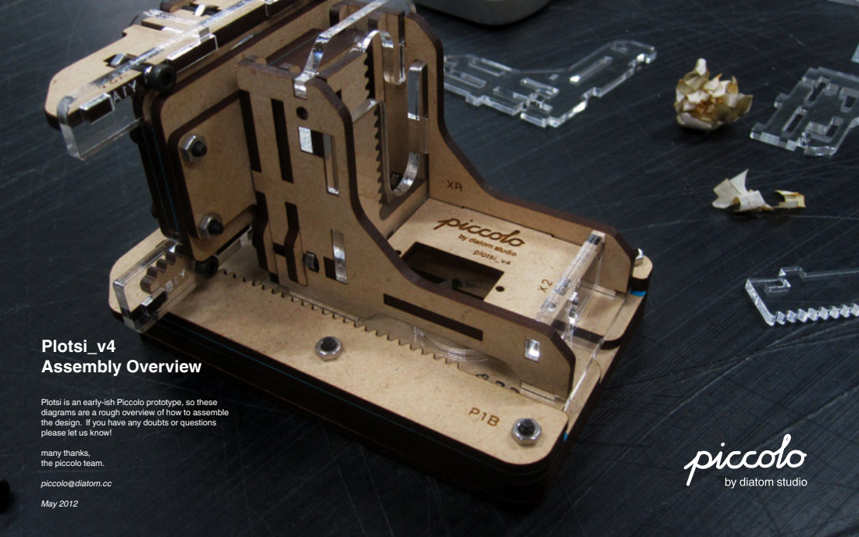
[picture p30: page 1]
Plotsi_v4 Assembly Overview

Plotsi is an early-ish Piccolo prototype, so these
diagrams are a rough overview of how to assemble
the design. If you have any doubts or questions
please let us know!
many thanks,
the piccolo team.
piccolo@diatom.cc
May 2012

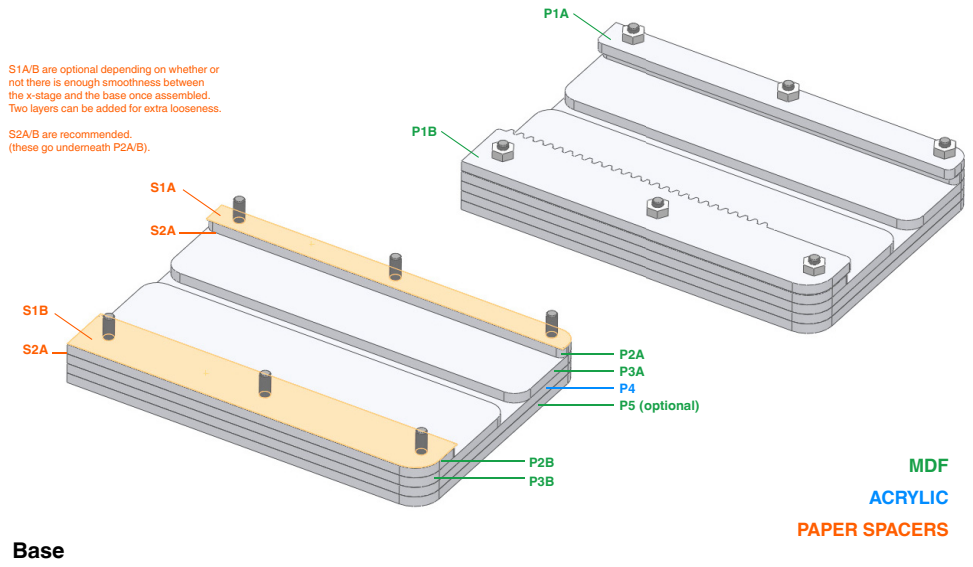
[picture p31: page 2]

S1A/B are optional depending on whether or
not there is enough smoothness between
the x-stage and the base once assembled.
Two layers can be added for extra looseness.
S2A/B are recommended.
(these go underneath P2A/B).

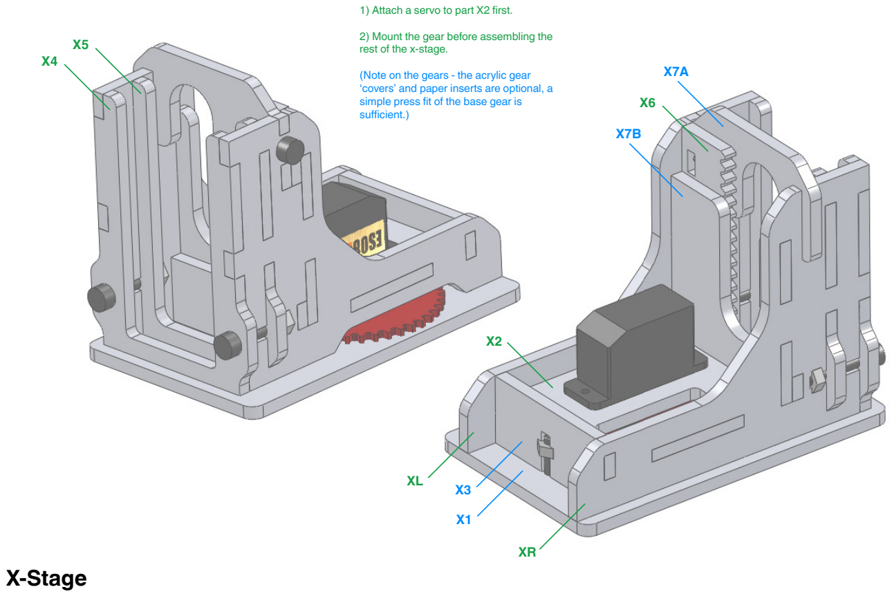
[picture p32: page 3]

XL

# X-Stage

1) Attach a servo to part X2 first.
2) Mount the gear before assembling the rest of the x-stage.
(Note on the gears - the acrylic gear ‘covers’ and paper inserts are optional, a simple press fit of the base gear is sufficient.)

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
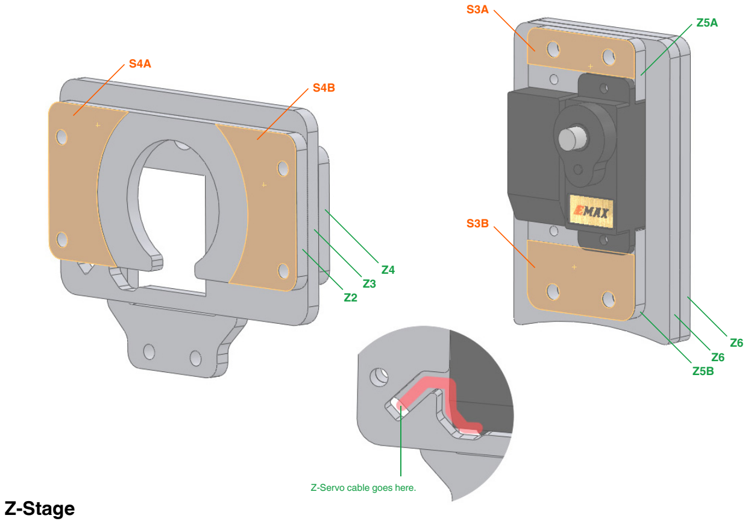
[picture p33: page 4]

# Z-Stage

S3A

Z-Servo cable goes here.

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
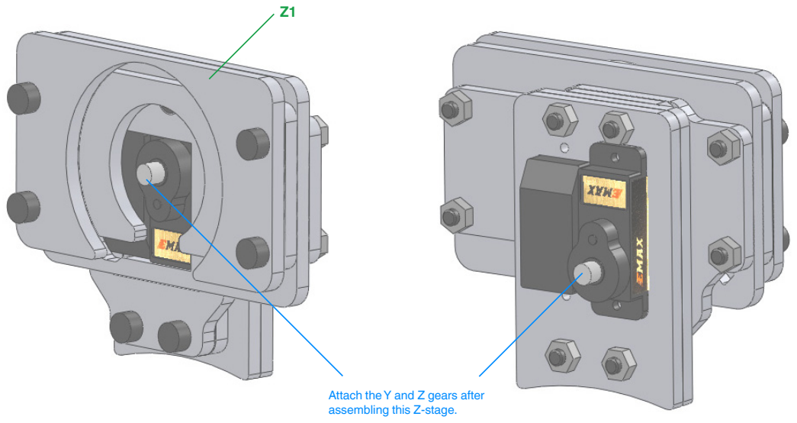
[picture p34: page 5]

Attach the Y and Z gears after assembling this Z-stage.

Z1

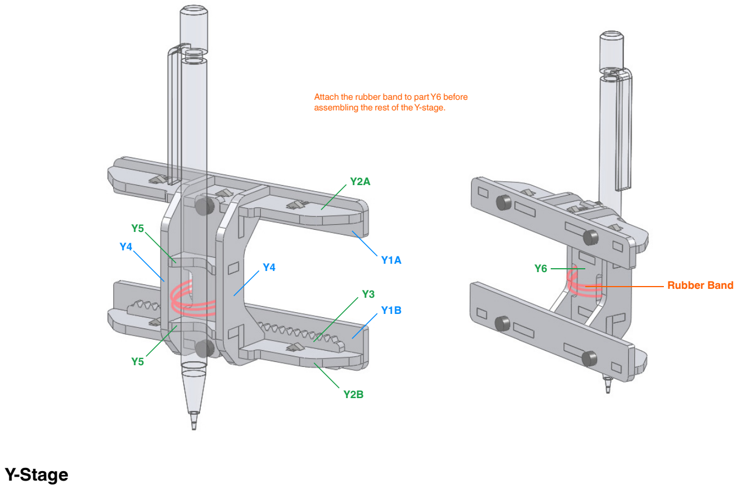
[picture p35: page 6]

# Y-Stage

Attach the rubber band to part Y6 before assembling the rest of the Y-stage.

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
### Rubber Band

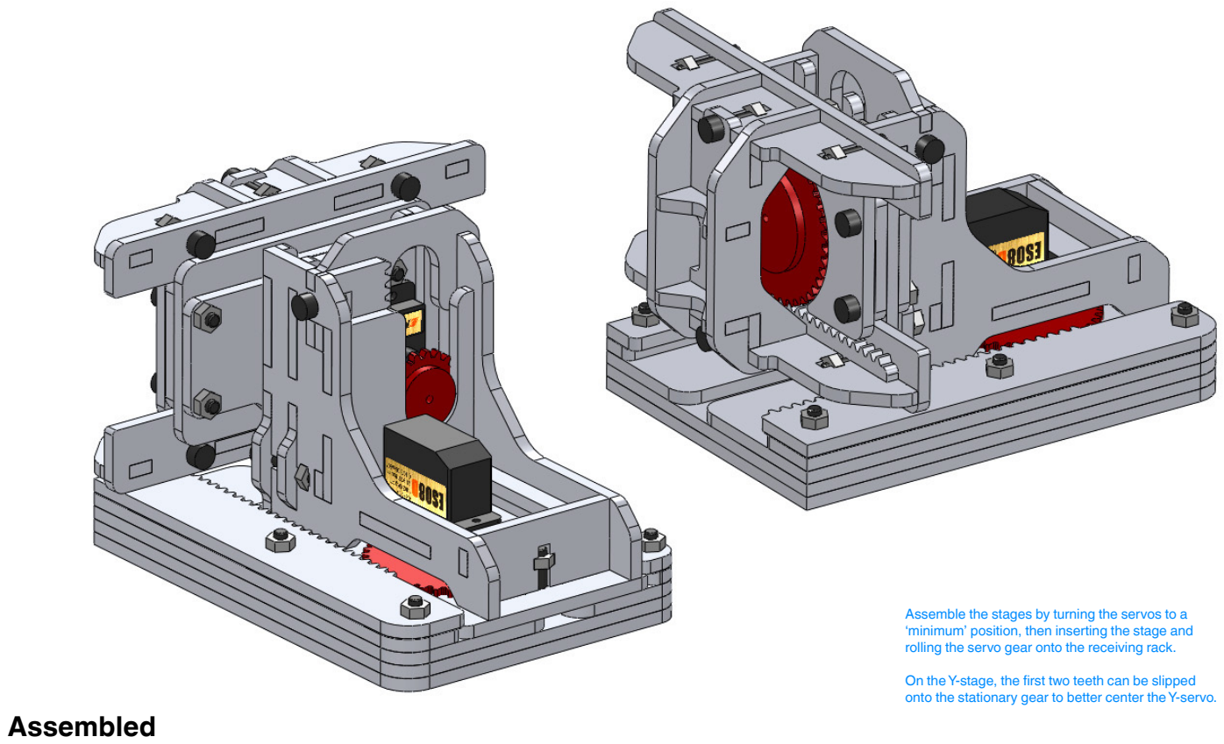
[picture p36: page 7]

# Assembled

Assemble the stages by turning the servos to a ‘minimum’ position, then inserting the stage and rolling the servo gear onto the receiving rack.
On the Y-stage, the first two teeth can be slipped onto the stationary gear to better center the Y-servo.

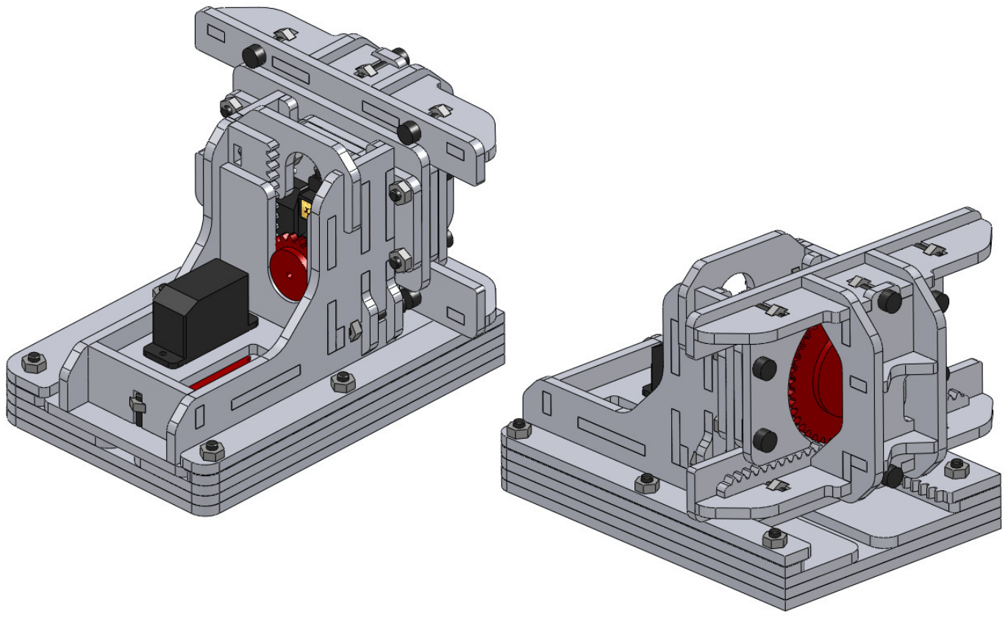
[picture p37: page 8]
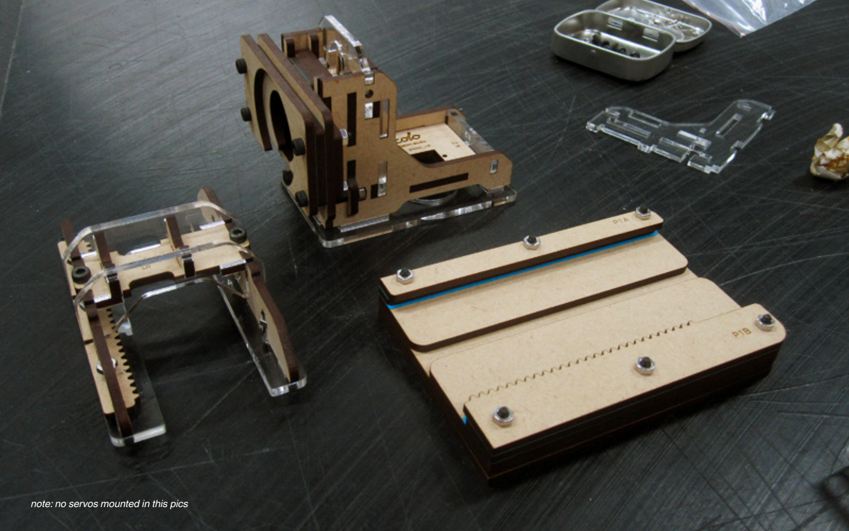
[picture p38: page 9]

### note: no servos mounted in this pics

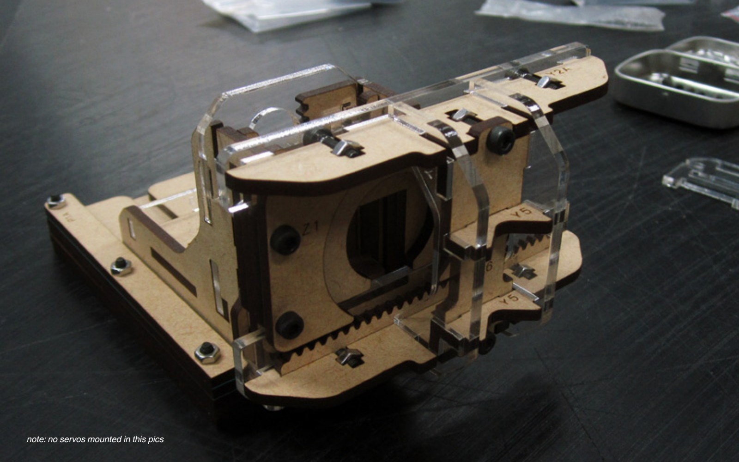
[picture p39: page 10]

### note: no servos mounted in this pics

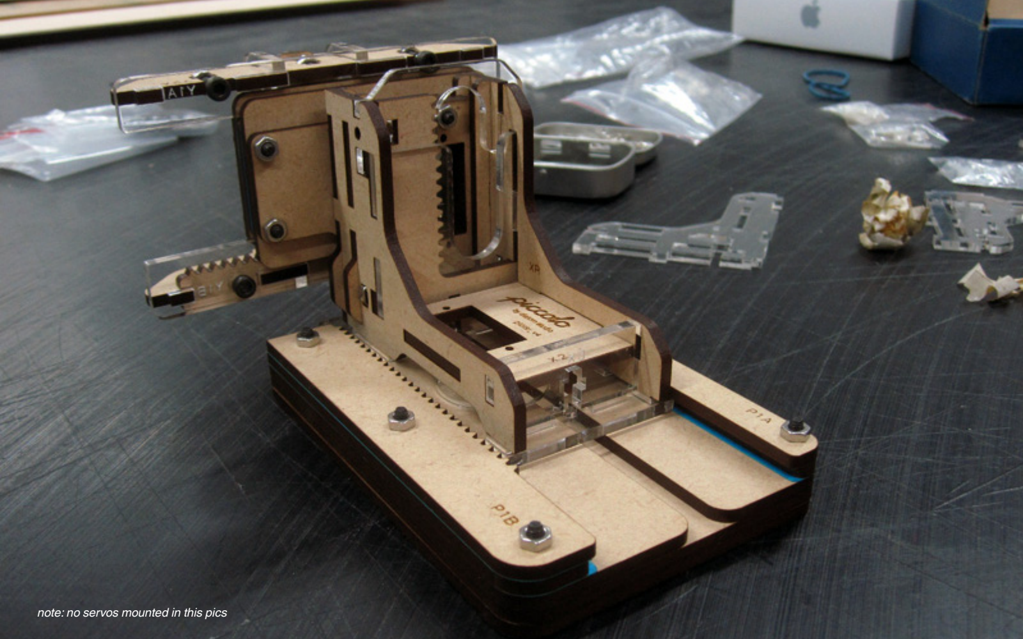
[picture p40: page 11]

### note: no servos mounted in this pics

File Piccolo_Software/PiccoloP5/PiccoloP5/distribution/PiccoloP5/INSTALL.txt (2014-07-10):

How to install library Piccolo P5

Install with the "Add Library..." tool

New for Processing 2.0: Add contributed libraries by selecting "Add Library..." 
from the "Import Library..." submenu within the Sketch menu. Not all available 
libraries have been converted to show up in this menu. If a library isn't there,
it will need to be installed manually by following the instructions below.

Manual Install

Contributed libraries may be downloaded separately and manually placed within 
the "libraries" folder of your Processing sketchbook. To find (and change) the 
Processing sketchbook location on your computer, open the Preferences window 
from the Processing application (PDE) and look for the "Sketchbook location" 
item at the top.

Copy the contributed library's folder into the "libraries" folder at this 
location. You will need to create the "libraries" folder if this is your first 
contributed library.

By default the following locations are used for your sketchbook folder: 
  For Mac users, the sketchbook folder is located inside ~/Documents/Processing. 
  For Windows users, the sketchbook folder is located inside 
    'My Documents'/Processing.

The folder structure for library Piccolo P5 should be as follows:

Processing
  libraries
    Piccolo P5
      examples
      library
        Piccolo P5.jar
      reference
      src
                      
Some folders like "examples" or "src" might be missing. After library 
Piccolo P5 has been successfully installed, restart the Processing 
application.

If you're having trouble, have a look at the Processing Wiki for more 
information: http://wiki.processing.org/w/How_to_Install_a_Contributed_Library

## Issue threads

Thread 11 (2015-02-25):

Piccolo issue

Josephhines, 2015-02-25:
My piccolo is fully assembled to the specs [with ardunio uno]. However, when I run the tether usb sketch the cnc slowly moves around [mostly jerking motions in the Z axis] but never moves on to the test circles when i press the test button.

When i try to upload another drawing via controllo there is no discernable change. any thoughts?

any update as to when a help forum will be established? [the link is dead on the site]

gregsaul, 2015-02-25:
Hi Joseph,

This potentially sounds like a issue caused by electrical noise from the servo's. Could you try adding  nice big capacitor between 5V and GND on your Arduino?

Greg

Josephhines, 2015-03-21:
Hey Greg,

I currently have a 330uF 25v capacitor in place. still struggling  with the same issues. Any other thoughts?

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

Closed 2015-03-27.

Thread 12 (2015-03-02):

Solution to stop bottom gear from falling off?

Powder, 2015-03-02:
I already posted this on Discqus, but probably it’s better to have it here …

>I have one problem with the gears. Because I had to disassemble the unit a lot of times to make the gears and teeth go smoothly, the bottom gear is falling off after a short time. For a future version it would be nice to have something to prevent that.
Btw. I used 3mm MDF and 3mm acrylic glass, will try to make new gears with less than 3mm.

Answer from Greg:

>The gear falling off can be a bit of a problem as at the moment we rely on friction to hold it . Currently the best way to fix this is either to try re-cutting the gear with a smaller spline until it fits snugly or to glue it on with something like superglue. But in future versions it would be good to fix this correctly. Cutting the gear from 2mm acrylic is also a good idea, sometimes this works well with a 3mm acrylic but if the MDF is slightly thinner than the acrylic it will catch.

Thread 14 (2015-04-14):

Z-Axis not working using Controllo

kgolinski, 2015-04-14:
I have assembled two piccolos, and uploaded latest usbTether. Adjusting the height of the pen works using the pot, but when drawing using Controllo the pen stays down all the time. What might be causing it?

Closed 2020-03-17.

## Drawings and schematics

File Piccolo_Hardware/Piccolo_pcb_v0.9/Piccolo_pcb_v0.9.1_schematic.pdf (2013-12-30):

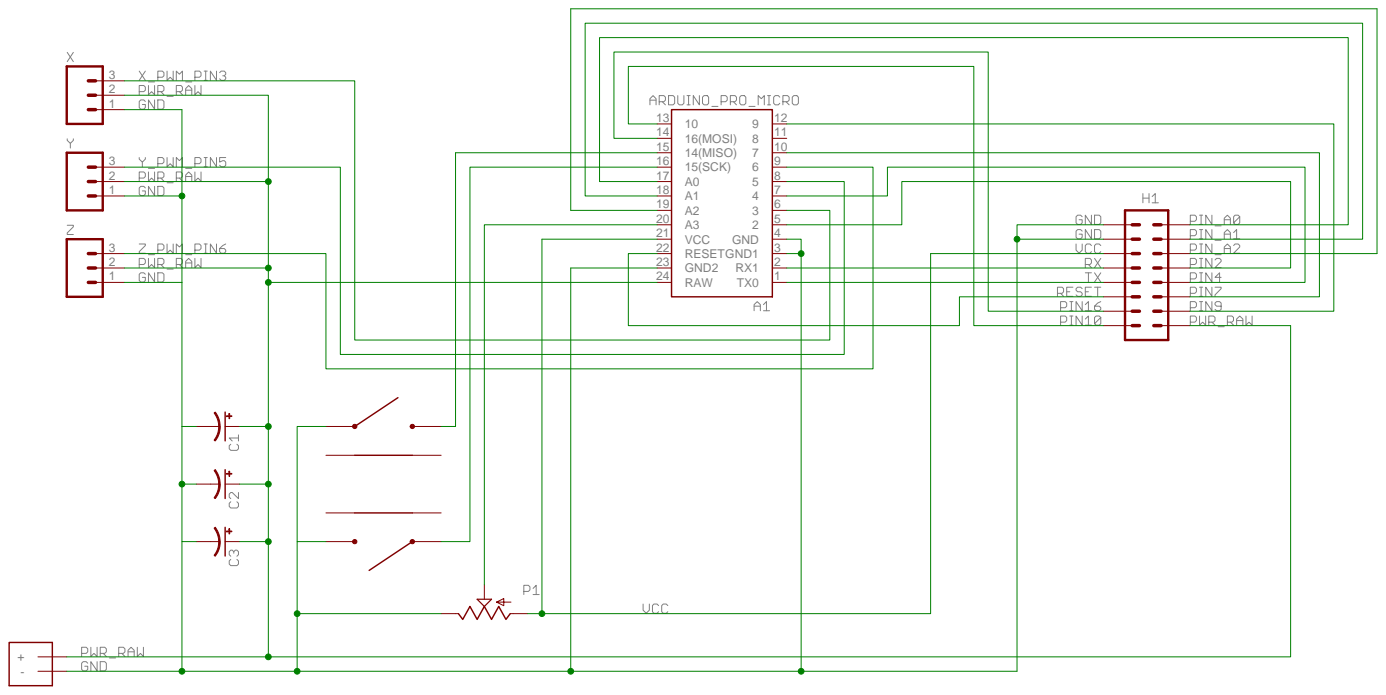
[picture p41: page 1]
16(MOSI) 14; 14(MISO) 15; 15(SCK) 16; GND; GND2 23 RAW 24; GND1; 3 RESET 22; VCC 21

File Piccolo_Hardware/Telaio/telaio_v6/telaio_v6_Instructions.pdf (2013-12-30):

## Telaio v6 Assembly Diagrams

## X-Stage

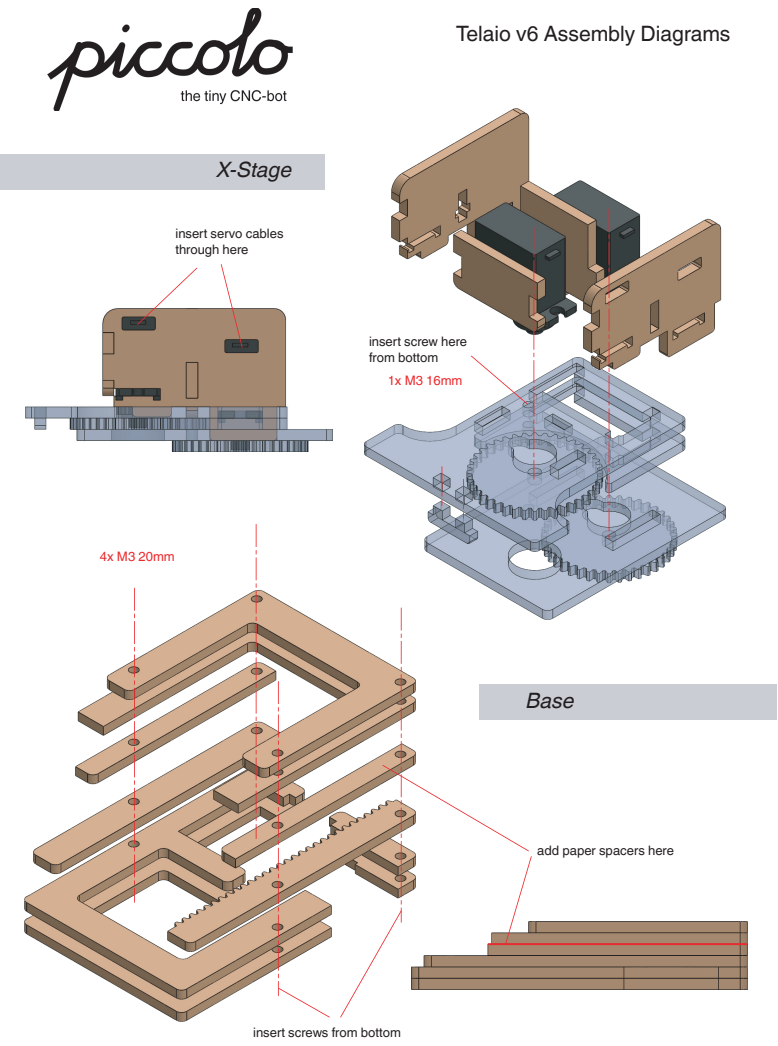
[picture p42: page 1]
Base

insert servo cables
through here

insert screw here
from bottom

add paper spacers here

insert screws from bottom

## Y-Stage

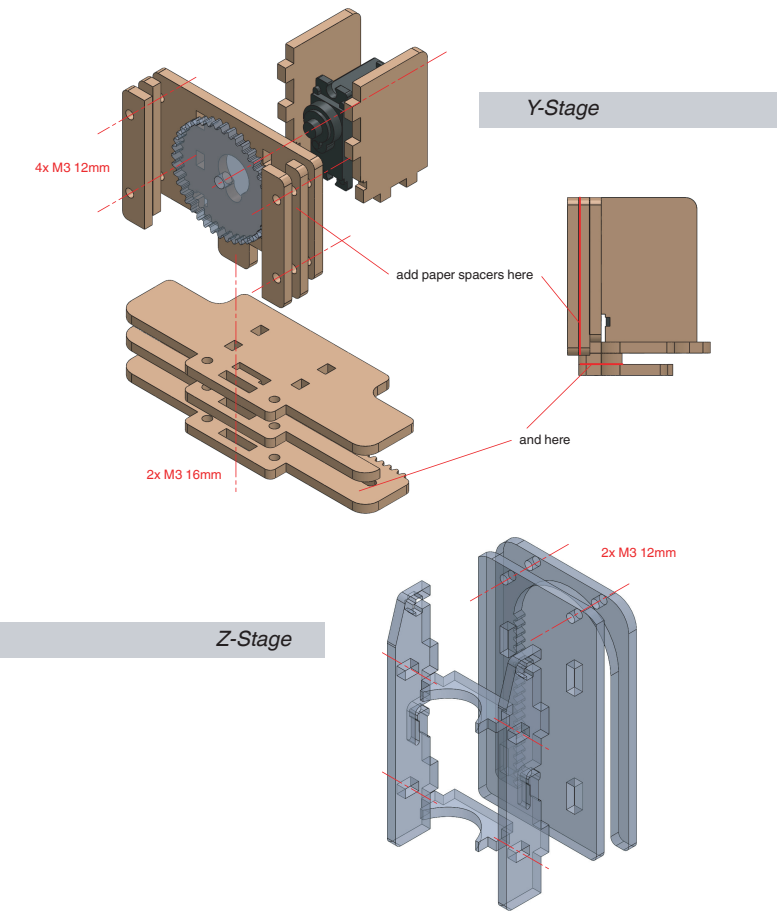
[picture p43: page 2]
Z-Stage; and here

add paper spacers here

## Arduino & Base-plate

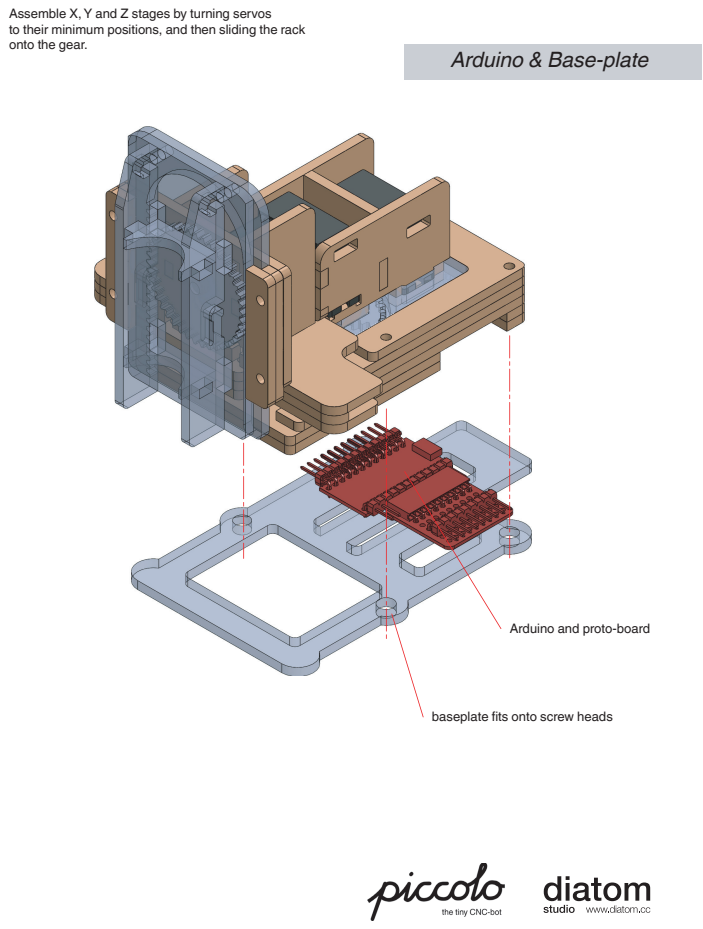
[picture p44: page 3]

Assemble X, Y and Z stages by turning servos
to their minimum positions, and then sliding the rack
onto the gear.

Arduino and proto-board

baseplate fits onto screw heads

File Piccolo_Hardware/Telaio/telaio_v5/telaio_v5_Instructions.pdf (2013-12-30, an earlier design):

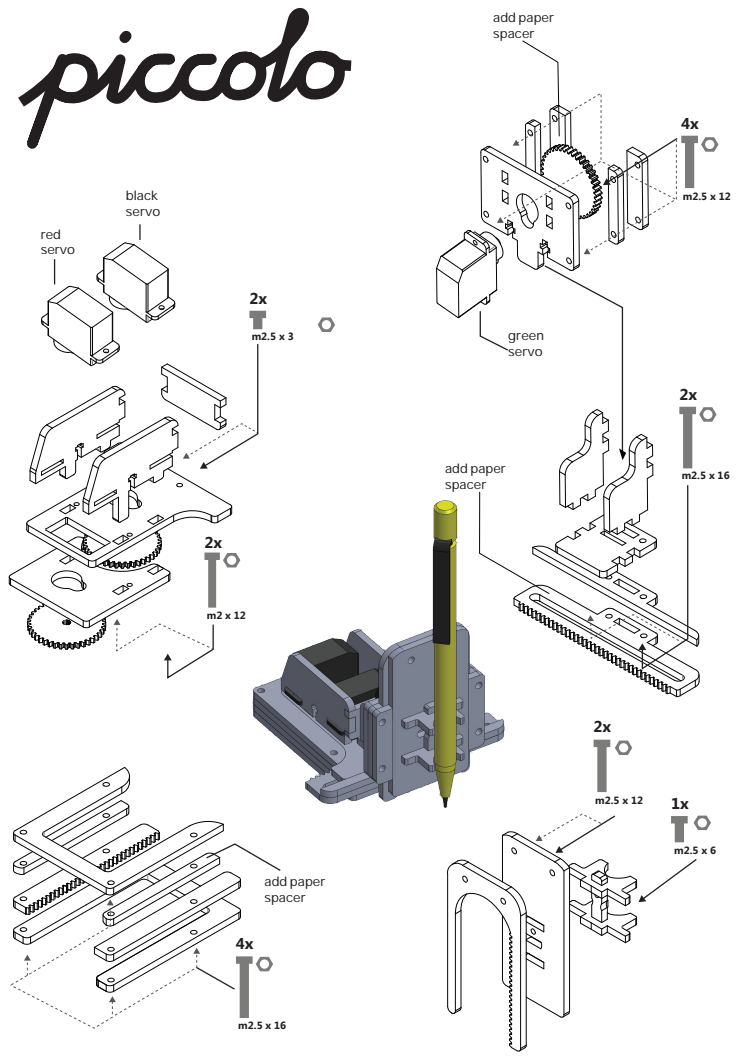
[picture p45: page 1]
add paper spacer; m2.5 x 16 add paper spacer; green servo; black servo; red servo

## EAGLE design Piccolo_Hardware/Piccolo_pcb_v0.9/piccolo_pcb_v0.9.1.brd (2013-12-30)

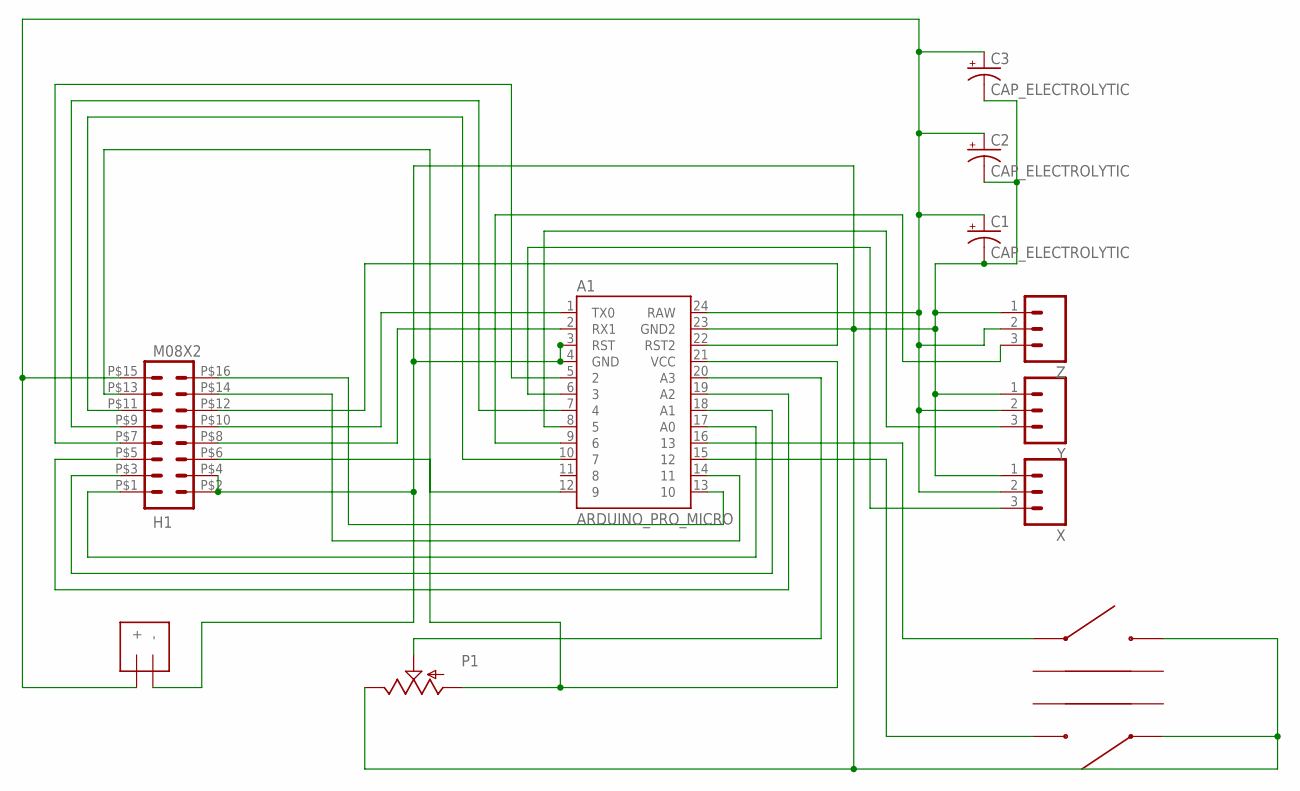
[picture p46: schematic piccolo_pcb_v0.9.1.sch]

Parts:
A1: ARDUINO_PRO_MICRO; ARDUINO_MINI
C1, C2, C3: CAP_ELECTROLYTIC; RADIAL_330UF
DC_IN: 4.8v-6.0v; JST-PH-2-PTH
H1: M08X2; PTH_2X8_90DEG_FEMALE
P1: POTTHUMBWHEEL; 16MM_THUMBWHEEL
S1, S2: SWITCH_TACTILE; RIGHT_ANGLE_TACTSWITCH
X: M03PTH; 1X03
Y: M03PTH; 1X03
Z: M03PTH; 1X03

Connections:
A3: A1.20 (A3), P1.P$2 (S)
GND: A1.3 (RST), A1.4 (GND), A1.23 (GND2), C1.C (-), C2.C (-), C3.C (-), DC_IN.-, H1.P$2 (2), H1.P$4 (4), P1.P$1 (E), S1.1, S2.2, X.1, Y.1, Z.1
unnamed: A1.15 (12), S1.2
unnamed: A1.16 (13), S2.1
PIN2: A1.5 (2), H1.P$7 (7)
PIN4: A1.7 (4), H1.P$9 (9)
PIN7: A1.10 (7), H1.P$11 (11)
PIN9: A1.12 (9), H1.P$13 (13)
PIN10: A1.13 (10), H1.P$16 (16)
PIN16: A1.14 (11), H1.P$14 (14)
PIN_A0: A1.17 (A0), H1.P$1 (1)
PIN_A1: A1.18 (A1), H1.P$3 (3)
PIN_A2: A1.19 (A2), H1.P$5 (5)
PWR_RAW: A1.24 (RAW), C1.A (+), C2.A (+), C3.A (+), DC_IN.+, H1.P$15 (15), X.2, Y.2, Z.2
RESET: A1.22 (RST2), H1.P$12 (12)
RX: A1.2 (RX1), H1.P$8 (8)
TX: A1.1 (TX0), H1.P$10 (10)
VCC: A1.21 (VCC), H1.P$6 (6), P1.P$3 (A)
X_PWM_PIN3: A1.6 (3), X.3
Y_PWM_PIN5: A1.8 (5), Y.3
Z_PWM_PIN6: A1.9 (6), Z.3

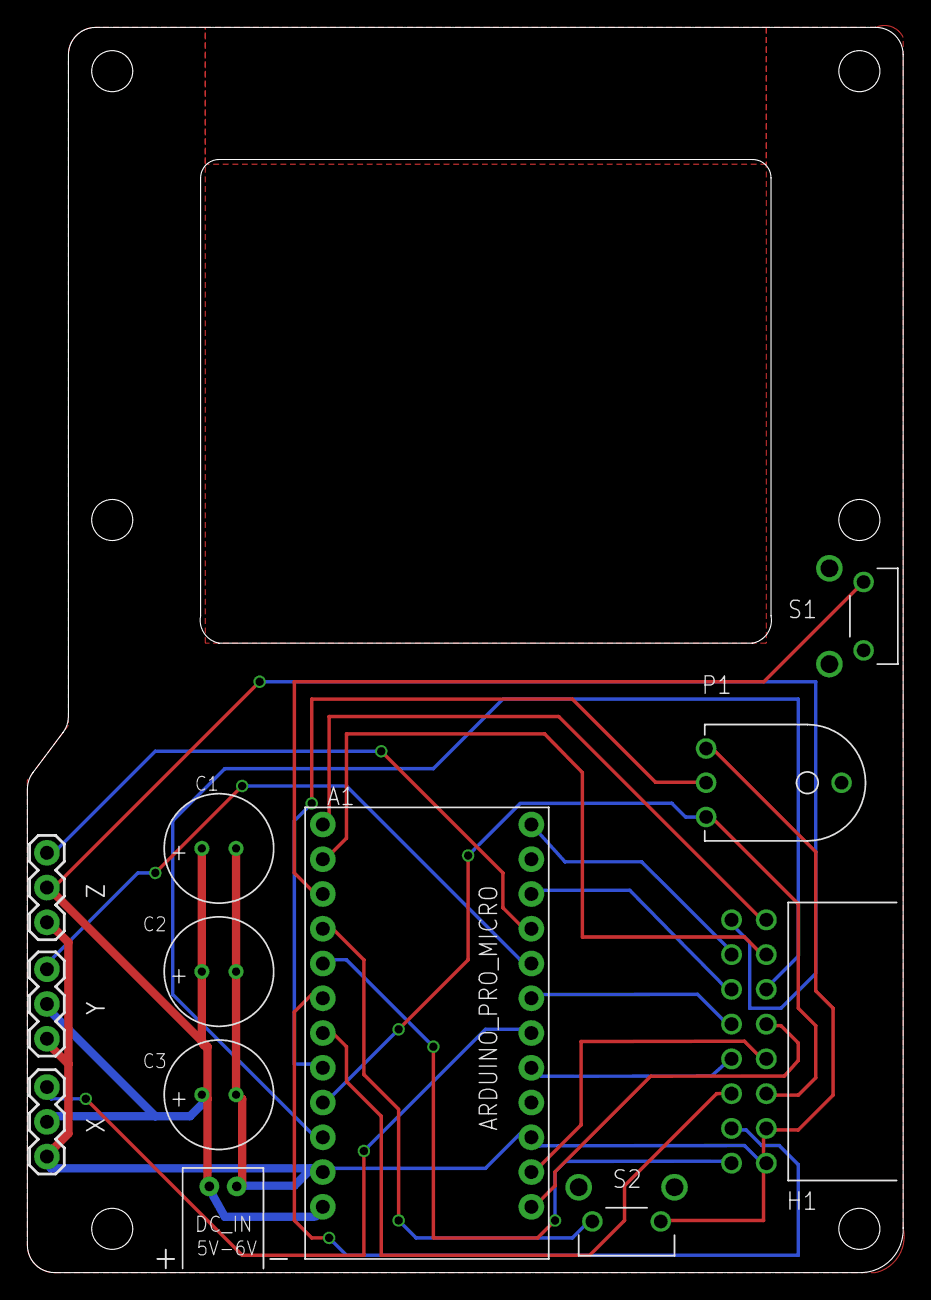
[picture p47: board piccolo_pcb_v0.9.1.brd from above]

Board: 2 copper layers, 64.0 x 91.0 mm, 12 parts (0 on the bottom side), 21 nets.

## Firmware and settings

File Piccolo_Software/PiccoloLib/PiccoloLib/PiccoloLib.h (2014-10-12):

/*
 PiccoloLib.h - Library for controlling Piccolo the tiny CNC-bot.
 Piccolo.cc
 Created by Diatom Studio, October 10, 2013.
 Released into the public domain.
 */


#ifndef PiccoloLib_h
#define PiccoloLib_h

/*Includes*/
#include "Arduino.h"
#include <Servo.h> //requires Servo.h to run.

/*Setup IO pins*/
#define THUMBWHEEL_PIN A3
#define BUTTON_ONE_PIN 14
#define BUTTON_TWO_PIN 15
#define SERVO_X_PIN 3
#define SERVO_Y_PIN 5
#define SERVO_Z_PIN 6

/* 
    SERVO VARIABLE HIERARCHY:

    uS = pulse width in microseconds of signal sent to the servo.

    1)      uScenter
        defines the center position of the servo, based on where we want
        piccolo think the center is.  Normally this would be mid-way between the
        minimum and maximum rotation of the servo.

            bedSize
        We define what we want the bed size to be.  The default is 50mm, which is a
        conservative size that should fit within the range of most DS929-MG servos.
    
            uSdeg
        We specify the change in uS per degree of rotation for the servo. This can be
        calibrated as in 5).    

            gearSize
        We specify the gear pitch diameter based on the actual pinion gear dimensions.
        

    2)  The gear pitch diameter and the change in uS per degree are used to calculate
        the change in uS per mm of motion:

            uSmm = uSdeg/((PI/360)*gearSize)
    
    3)  The uS range is found by multiplying the bed size by the uS/mm

            uSrange = bedSize * uSmm

    4)  The uS minimum and maximums are found by using the uS range and center

            uSmin = uScenter - (uSrange/2)
            uSmax = uScenter + (uSrange/2)

    5) uSdeg can be calibrated by drawing a target dimension and measuring the actual output

            uSdeg  = ((target*uSmm)/actual) * (PI/360)*gearSize;

*/

/*Servo Defaults*/
#define DEFAULT_USCENTER 1551  // center position of servo in uS
#define DEFAULT_BEDSIZE  50.0  // bed size in mm
#define DEFAULT_USDEG    9.7   // change in uS per degree of rotation
#define DEFAULT_GEARSIZE 35.23 // gear pitch diameter

/*Drawing Defaults*/
#define DEFAULT_STEP_SIZE 0.1  // in mm.
#define DEFAULT_SPEED 60       // in mm per second
#define DEFAULT_PEN_UP_POS 5   // in mm, relative to center
#define DEFAULT_PEN_DOWN_POS -5

/*Draw Orientations from piccolo's perspective*/
#define ORIENTATION_LEFT   0   // default, drawing with bottom of drawing to the left
#define ORIENTATION_TOP    1   // top, as if piccolo is draw upside down
#define ORIENTATION_RIGHT  2   // right, drawing with bottom of drawing to the right
#define ORIENTATION_BOTTOM 3   // bottom, as if piccolo is draw the correct way up

/* Command Bytes */
#define  COMMAND_CONNECT          'C'    //connect byte                      from computer       
#define  COMMAND_SEND_NEXT        'B'    //send the next packet              from piccolo
#define  COMMAND_READY            'A'    //piccolo ready to plot!            from piccolo
#define  COMMAND_POS_START_BYTE   'P'    //start of position                 from computer
#define  COMMAND_POS_END_BYTE     ';'    //end of position                   from computer
#define  COMMAND_END_STACK        'E'    //finished sending current stack.   from computer      


class PiccoloAxis
{ 
public:
    PiccoloAxis();

    Servo servo;

    /* setup functions */
    void setup(int _pin);
    void setup(int _pin, int _uScenter, float _bedSize);
    void setup(int _pin, int _uScenter, float _bedSize, float _uSdeg);
    void setup(int _pin, int _uScenter, float _bedSize, float _uSdeg, float _gearSize);
    void setup(int _pin, int _uScenter, float _bedSize, float _uSdeg, float _gearSize, boolean _inverted);

    void calcuSdeg(float target, float actual);
    void calcuSmm();
    void calcuSrange();
    void calcMinMax();

    void invert(boolean _inverted);  
    void moveCenter(float offset);
    void setBedSize(float newSize);

    /* mechanical functions */
    void move(float _pos);

    /* get variables */
    int   getPin();
    int   getuScenter();
    float getuSdeg();
    float getGearSize();
    float getBedSize();

    float getuSmm();
    int   getuSrange();
    int   getuSmin();
    int   getuSmax();

    float getPos();
    boolean isInverted();

    // Advanced (to do)
    /*
    float setuSmm(float _uSmm);
    int   setuSrange(int _uSrange);
    int   setuSmin(int _uSmin);
    int   setuSmax(int _uSmax);
    */

private:

    int   pin;
    int   uScenter;
    float bedSize;
    float uSdeg;
    float gearSize;

    float uSmm;
    int   uSrange;
    int   uSmin;
    int   uSmax;

    float pos;
    boolean inverted;

};


class PiccoloLib
{
public:

    PiccoloLib();
    
    PiccoloAxis X;
    PiccoloAxis Y;
    PiccoloAxis Z;

    /* setup functions */
    void setup(); // Sets up X,Y,Z axes with default settings.
    void setup(int xPin, int yPin, int zPin); // setup using custom pin assignments
    void invert(boolean invertX, boolean invertY, boolean invertZ);
    void moveCenter(float xOffset, float yOffset);
    void moveCenter(float xOffset, float yOffset, float zOffset);
    void calibrate(float targetDimension, float actualX, float actualY);
    void calibrate(float targetDimension, float actualX, float actualY, float actualZ);

    void setBedSize(float size);
    void setBedSize(float xySize, float zSize);
    void setBedSize(float xSize, float ySize, float zSize);
    void setSpeed(float speed);             //in mm per seconds
    void setStepSize(float _stepSize);      //default is 0.1mmm
 
    /* mechanical functions */
    void moveX(float x);
    void moveY(float y);
    void moveZ(float z);
    void move(float x, float y);
    void move(float x, float y, float z);
    void setDrawOrientation(int _orientation);
    void home();

    //tentative
    void thumbwheelControlX();
    void thumbwheelControlY();
    void thumbwheelControlZ();
    //boolean thumbwheelZcontrol;

    void setPenDownPos(float _penDownPos);
    float getPenDownPos();

    /* piccolo brain inputs */
    float readThumbwheel();
    boolean buttonOneDown();
    boolean buttonTwoDown();
 
    /* serial functions */   
    void serialSetup();
    void serialLoop();   
    
    /* draw functions */
    void beginShape();
    void endShape();
    void vertex (float x,  float y);
    void vertex (float x,  float y,  float z);
    void line   (float x1, float y1, float x2, float y2);
    void line   (float x1, float y1, float z1, float x2, float y2, float z2);
    void rect   (float x,  float y,  float width, float height);
    void rect   (float x,  float y,  float z, float width, float height);
    void ellipse(float x,  float y,  float width, float height);
    void arc    (float x , float y , float width, float height, float startA, float stopA);
    void bezier   (float x1, float  y1, float  cx1, float  cy1, float  cx2, float  cy2, float  x2, float  y2);
    void bezierYZ (float x1, float  y1, float  cx1, float  cy1, float  cx2, float  cy2, float  x2, float  y2);     
    float bezierPoint  (float a, float b, float c, float d, float t);
    float bezierTangent(float a, float b, float c, float d, float t);

    boolean serialStream;    // Streams coordinates over Serial as G-Code
    boolean disableMotion;   // disables servo motion, for debugging purposes
    int drawOrientation;     // Piccolo's current draw orientation. 

    
private:

    // These control piccolo speed and level of detail
    float stepSize;       // Motion between two points is divided into segments to control speed.
                          // A smaller step size means a more controlled motion, but too small will limit the maximum speed.
                          // Also affects curvature when using ellipse(), arc(), or bezier(); smaller stepSize means a less faceted curve
    float mmPerSecond;    // speed in mm per second.
    int delayPerStep;     // delay in milliseconds, calculated based on speed and stepSize.
                          // longer delay means more time for the servo to reach its target position.
    void calcDelayPerStep();

    // The pen positions for pen-up (lifted) and down (drawing)
    float penUpPos;
    float penDownPos;
    
    boolean beginDrawFlag; // For moving the pen into position before starting to draw
  	boolean drawing;       // If the pen is touching the paper

  	float dist(float x1, float y1, float z1, float x2, float y2, float z2);
    float dist(float dx, float dy, float dz);

    //float calcFloat(char *str);
    //float calcFloat(int data[], int ind);
    float calcFloat(byte b_1, byte b_2, byte b_3, byte b_4);


	/* Serial functions */
    //void establishContact();
    #define CHAR_PER_POS 8
    byte inByte;
	byte inString[25];  // xxxxxxxxyyyyyyyzzzzzzzz;
    byte tmpPosStr[CHAR_PER_POS];  //copy inString into this for converting from HEX
	int index;
	boolean gotPos;
    boolean waitingForPos;

};


#endif

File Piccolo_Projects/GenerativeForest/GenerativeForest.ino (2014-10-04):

#include <Servo.h>
#include <PiccoloLib.h> //include the Piccolo Lib


PiccoloLib piccolo; //Make a instance of the Piccolo library for controlling Piccolo

int LDR_PIN = A2; 
float LDR_TOP_LIMIT = 612.0; //value when sensor is covered; 

unsigned long tstBtnDwnTime;
unsigned long lastThumbChange;

float THUMB_ACTIVATE_THRESHHOLD = 30.0f;
float THUMB_CHANGE_THRESHHOLD = 5.0f;
boolean btnOneDown;


float sentZHeight = 0; 
float prevThumbWheelVal; 
float lightReadingStart;

void setup() {
  piccolo.setup(); //Setup Piccolo
  piccolo.setDrawOrientation(ORIENTATION_BOTTOM); //draw with the picture facing piccolo 
  piccolo.home(); //Tell Piccolo to goto it's home position. 
  btnOneDown = false;
  
  tstBtnDwnTime = 0;
  lastThumbChange = 0;
  prevThumbWheelVal = 0;
  
}

void loop() {

  
  // Is button two down and has been held down for more than 2 seconds?
  if(piccolo.buttonTwoDown() && millis() - tstBtnDwnTime > 2000){
    LDR_TOP_LIMIT = analogRead(LDR_PIN);
    Serial.print("Set LDR_TOP_LIMIT to: ");
    Serial.println(LDR_TOP_LIMIT);
    piccolo.home();
    tstBtnDwnTime = 0;
  }


   //Use the Piccolo thumbwheel to set the Z draw height for piccolo and relay this over the serial
   float val = piccolo.readThumbwheel();
   float deltaVal = abs(prevThumbWheelVal-val);

   if( deltaVal > THUMB_ACTIVATE_THRESHHOLD || (millis() - lastThumbChange < 1000 && deltaVal > THUMB_CHANGE_THRESHHOLD)){
     lastThumbChange  = millis();
     prevThumbWheelVal = val;
     float zVal = ((piccolo.Z.getBedSize()/1024.0)*val)-(piccolo.Z.getBedSize()/2.0);
     piccolo.move(piccolo.X.getPos(), piccolo.Y.getPos(),zVal);
     piccolo.setPenDownPos(zVal);
 
     //Send new Z height of serial
     Serial.print("setZ:");
     Serial.print(zVal);
     Serial.println();
   }
  
  
  
  
    if(!btnOneDown && piccolo.buttonOneDown()){

     lightReadingStart =  1.0 - (analogRead(LDR_PIN) / LDR_TOP_LIMIT);
    Serial.print("light reading: ");
    Serial.println(lightReadingStart);
    
    //lightReading = constrain(lightReading,0.25,0.5);
    generatePlant(lightReadingStart);

   }
  
  btnOneDown = piccolo.buttonOneDown();
  
}

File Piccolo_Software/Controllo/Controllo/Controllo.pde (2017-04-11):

/*
Controllo 
by: Diatom Studio , 2013

This program controls and sends drawing commands to a Piccolo teathered by a usb cable. 
All coodinates are sent in pixels/mm and are scaled for drawing to the screen. 
Coordinates are centred around XYZ at 0,0,0.
*/

/*
Notes:
- Should we separate plotsipiccolo. to it's own library?
- Could Controllo be a example in this library?
- Can we make seperate sketches / apps for generative drawings etc so that we can keep controllo clean and simple?
- If so how would a exhibition setup work? webpage to launch diff apps.
*/

//Libraries
import piccoloP5.*;

import controlP5.*;
import processing.serial.*;
import java.awt.FileDialog;
import geomerative.*;
import java.util.*;
import javax.swing.JOptionPane;

PVector prevDrawPoint = new PVector(0,0);

boolean view3D = false; // display view in 3D


//Piccolo bed size in mm
float bedWidth = 50.0; 
float bedHeight = 50.0; 
float bedDepth = 50.0; 
float bedRenderWidth = 300;

//current position of drawing command to send
float xPos = 0;          
float yPos = 0;      
float zPos = 0;  

boolean fitSVGtoBed = true;

public boolean drawTool = false;

//TODO: this should be removed or moved to make code more straight forward.
//sensor sets
public float lightLevel = 0.5;

PShape loadedSVG; //svg loaded for sending to piccolo.
/*
Currently loaded SVG is shown on screen until user presses start. 
At this point the SVG is loaded into the output canvas and sent to Piccolo. 
It might be a better idea to always load drawing shapes directly into the output 
canvas so that they always reflect what Piccolo is drawing. 
*/

List path = new ArrayList();

PiccoloP5 piccolo = new PiccoloP5(bedWidth,bedHeight,bedDepth);
ControlP5 controlP5;
CheckBox drawPlotsiOutput;
Knob pressureKnob;

PGraphics plotsiOutputCanvas; 







void setup() {
  size(500, 340,P3D);
  plotsiOutputCanvas = createGraphics((int)bedWidth, (int)bedHeight);
  plotsiOutputCanvas.beginDraw();
  plotsiOutputCanvas.smooth();
  plotsiOutputCanvas.endDraw();

  //canvas defaults
  piccolo.setStepRes(1f);
  piccolo.bezierDetail(20); 
  piccolo.rotate(PI/2.0f);
  
  //setup GUI
  controlP5 = new ControlP5(this);
  drawInterface();

  String s = (String) JOptionPane.showInputDialog(
      null,
      "Select Piccolo's COM Port",
      "Select Piccolo",
      JOptionPane.PLAIN_MESSAGE,
      null,
      Serial.list(),
      Serial.list()[Serial.list().length-1]
  );

  println(s);

  // List all the available serial ports
  //TODO: select serial port at this point. 
try{
  piccolo.serial = new Serial(this, s, 115200);
  piccolo.serial.bufferUntil('\n');
  piccolo.serialConnected = true;
}catch(Exception e){
  piccolo.serialConnected = false;

}
  

  // Initialise Geomerative for working with type.
  RG.init(this);
  delay(200);
  home();
}

//---------------------------- draw functions --------------------------------//

void draw() {

  
  background(255, 255, 255);
   // Commenting line below bo make it work on Processing 3.3
  // ortho(0, width, 0, height); // same as ortho()
  pushMatrix();
  translate((bedRenderWidth/2) + 150, (bedRenderWidth/2)+20,0);
  

  if(view3D){
    rotateX(PI/4.0);
    rotateZ(PI/4.0);
    translate(0,0,(bedRenderWidth/2));
   }

  stroke(0);
  noFill();

  pushMatrix();
  // Commenting line below bo make it work on Processing 3.3
  //translate(0,0,-(bedRenderWidth/2));
  rect(-(bedRenderWidth/2),-(bedRenderWidth/2),bedRenderWidth,bedRenderWidth);
  popMatrix();

  rotate(-PI/2.0f);
  piccolo.draw(g,bedRenderWidth);
  popMatrix();
  piccolo.update();
}



void mousePressed(){
  if(drawTool && mouseX > 150 && mouseX < 450 && mouseY > 20 && mouseY < 320){
    piccolo.beginShape();
  }
}


void mouseDragged(){
  if(drawTool && mouseX > 150 && mouseX < 450 && mouseY > 20 && mouseY < 320){
    
     float posX = (((mouseX - 150)/bedRenderWidth) * piccolo.bedWidth) - piccolo.bedWidth/2.0f;
     float posY = (((mouseY - 20)/bedRenderWidth)*piccolo.bedHeight) - piccolo.bedHeight/2.0f;


if(prevDrawPoint.dist(new PVector(posX,posY)) > 2){
    piccolo.vertex(posX,posY);
    prevDrawPoint = new PVector(posX,posY);
}
  }
}

void mouseReleased(){
    if(drawTool){
    piccolo.endShape();
    }
}



void keyPressed(){
  if(key == '3')
    view3D = true;

    if(key == '2')
    view3D = false;
}



public void penUp(int val) {
  piccolo.clear(); 
  piccolo.vertex(0 , 0, piccolo.getPenLiftHeight());
  piccolo.vertex(0, 0, piccolo.getPenLiftHeight());

  piccolo.start();
}

public void penDown(int val) {
  piccolo.clear(); 
  piccolo.vertex(0, 0, 0);
  piccolo.vertex(0, 0, 0);

  piccolo.start();
}







public void load_SVG(int val) {

  FileDialog fd = new FileDialog(frame, "open", 
  FileDialog.LOAD);
  String currentDir = new File(".").getAbsolutePath();


  fd.setLocation(50, 50);
  fd.pack();
  fd.show();

  if (fd.getName() != null) {

    String filename = fd.getFile();
    clearCanvas();
    PShape svg = loadShape(fd.getDirectory() + filename);
    svg.disableStyle();
    piccolo.beginDraw();
    piccolo.clear();
    piccolo.pushMatrix();

    float scaleSVG;

    if(fitSVGtoBed)
     scaleSVG = bedWidth / max(svg.width,svg.height);
    else
    scaleSVG = 0.16666666666667;
    
        piccolo.translate(-(piccolo.bedWidth/2.0),-(piccolo.bedHeight/2.0),0.0);

    piccolo.scale(scaleSVG);

    piccolo.shape(svg,0,0);
    piccolo.popMatrix();
    piccolo.endDraw();

    //loadedSVG.scale(0.6); 
    //
  } 
  else {
    // println("not an stl file");
  }
}




void clearCanvas() {
  plotsiOutputCanvas = createGraphics((int)bedWidth, (int)bedHeight);
  plotsiOutputCanvas.beginDraw();
  plotsiOutputCanvas.smooth();
  //plotsiOutputCanvas.background(255);
  plotsiOutputCanvas.endDraw();  
  loadedSVG = null;
}

/*

void up_() {
  piccolo.penDownHeight+=5;
  piccolo.penLiftHeight = piccolo.penDownHeight+40;
  piccolo.clear();
  piccolo.stepTo(0, 0, piccolo.penDownHeight);
  piccolo.establishContact();
  clearCanvas();
}

void down_() {
  piccolo.penDownHeight-=5;
  println(piccolo.penDownHeight);
  piccolo.penLiftHeight = piccolo.penDownHeight+40;
  piccolo.clear();
  piccolo.stepTo(0, 0, piccolo.penDownHeight);
  piccolo.establishContact();
  clearCanvas();
}
*/
void home() {
  piccolo.clear();
  piccolo.stepTo(0, 0, piccolo.getPenLiftHeight());
  piccolo.start();
 // clearCanvas();
}

  
public void start(int val) {
  piccolo.start();
}


void stop(){
 piccolo.clear();
}


public void Up(int val) {
  println("Up");
  piccolo.clear();
  piccolo.start();
  if (zPos<90)
  {
    zPos+=10;
    piccolo.stepTo(xPos, yPos, zPos);
  }
  print("myZ:");
  println(xPos);
  println(yPos);
  println(zPos);
}

public void Down(int val) {
  piccolo.clear();
  piccolo.start();
  if (zPos>10)
  {
    zPos-=10;
    piccolo.stepTo(xPos, yPos, zPos);
  }
  print("myZ:");
  println(xPos);
  println(yPos);
  println(zPos);
}



// =========================================================== //
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

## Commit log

2013-12-30 initial hardware commit
    + controllo & piccolo lib, sans readme
    [24tooth_gear.stl, 44tooth_gear.STL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]
2014-01-03 PiccoloLib v0.2
    Firmware version loaded on TEI backers Piccolo’s
2014-01-07 add plotsi readme
    [plotsi_v1.SLDASM]
2014-01-09 update STL rotations
    [plotsi_v1.STL]
2014-01-10 Reorganise directory structure, PiccoloLib README
    Reorganise directory structure
    Added licence files
    PiccoloLib README
    Small spelling fixes in documentation.
    [Controllo.pde, PiccoloLib.cpp, PiccoloLib.h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]
2014-01-14 adjust t-slot on x-chassis to fit low profile nut
2014-01-20 Fixing slow move on first vertex
    Fixing slow move on first vertex, adding new examples.
    [PiccoloLib.cpp, PiccoloLib.h]
2014-01-21 fix bug in Piccolo.calcFloat(), add controllo Win/Mac binaries
    [PiccoloLib.cpp]
2014-01-26 resize t-slots on x-chassis for low-profile nuts
2014-01-26 added pcb outline to cutting pattern
2014-04-16 Fixing control to work with new PiccoloLib (in progress)
    Modifying control to work with new PiccoloLib
    -Changed PiccoloLib class name back to PiccoloLib from Piccolo
    -implemented sending coordinate as 32 bit signed ints.
    [Controllo.pde, PiccoloLib.cpp, PiccoloLib.h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]
2014-05-31 Added to Portrait prig, added button detect to Piccolo Processing Lib
2014-10-04 Folder rearrange step 1
    New Projects folder
    Controllo has it’s own folder under Software
    Additional readme’s and code comments
2014-10-05 Portrait
    Fixing up portrait to work with new version of PiccoloP5.
    [Face.pde, Portrait.pde, capture.pde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]
2014-10-13 Piccolo IOT
    Added to PiccoloP5 the option of stream piccolo commands over Http
    instead of Serial, useful for sending piccolo commands from devices
    that do not have usb or serial ports.
    Added Android port of Control (work in progress)
    Small fixes in Controllo.
    [ControlloArduino.pde, PiccoloLib.cpp, PiccoloP5.java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]
2014-10-16 Removed incompatible examples.
    Removed incompatible examples PiccoloLib
    [spiral.ino]
2014-10-19 fixed math in ellipse & arc
    [PiccoloLib.cpp]
2015-02-06 Fixed syntax error
    extra 'x' found during a VHS workshop ;-)
    [PiccoloLib.cpp]

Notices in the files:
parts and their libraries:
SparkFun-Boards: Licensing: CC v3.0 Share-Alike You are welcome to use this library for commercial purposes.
